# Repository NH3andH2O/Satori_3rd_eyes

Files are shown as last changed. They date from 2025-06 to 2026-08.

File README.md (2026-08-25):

English | [简体中文](README_zh-cn.md) | [繁體中文](README_zh-tw.md) | [日本語](README_ja.md)

# Mechanical Satori's Third Eye

A mechanical version of Satori Komeiji's third eye from Touhou Project. It currently supports gyroscope tracking and web-based control.

## Demo

https://www.bilibili.com/video/BV137yHB4ERo

## Authors and Licenses

- Code: 一水合氨基酸 (NH3andH2O), licensed under `Apache-2.0`
- 3D models
    - Third-eye assembly `3rd_eyes`: 牧鈴華SUZUKA. The original author granted permission to upload it to this GitHub repository. Contact the original author before using it for any other purpose ([project page](https://www.bilibili.com/video/BV1rN1gYJE3K)).
    - Heart-shaped accessory `heart_shaped`: 一水合氨基酸, licensed under `CC BY 4.0`
- PCD
    - `3rd_eyes`: Modified from a design by R饼锐度不够, licensed under `CC BY-NC-SA 3.0` ([project page](https://oshwhub.com/flanker-e/jue-zhi-tong-esp32))
    - `GC9A01`: 一水合氨基酸, licensed under `CC BY-NC-SA 3.0`

## Asset Credits

- Third-eye web interface icon: 幽蝶_Zomgel

## Project Structure

- `3d_model`: 3D models
- `pcd`: PCD design files
- `code`: Source code
- `tools`: Tools for debugging device sensors

## Getting Started

Download this repository and read the README in each directory.  
Recommended order: [pcd](pcd/README.md) → [3d_model](3d_model/README.md) → [code](code/README.md)

## Controls

- After uploading the firmware, the device enters gyroscope-tracking mode by default. Attach the heart-shaped accessory to your head and secure the third eye to your body to control it.
- To change the settings, connect to the `3rd-Eyes` Wi-Fi network (no password), then open `3rdeyes.local` to change the control mode and settings.

## Roadmap

- Add autonomous third-eye movements, such as blinking and head shaking
- Add controller support

## Contact

Join the project QQ group: `727559409`

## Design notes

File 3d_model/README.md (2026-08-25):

English | [简体中文](README_zh-cn.md) | [繁體中文](README_zh-tw.md) | [日本語](README_ja.md)

# Mechanical Satori's Third Eye Models

## Other Authors

- **3rd_eyes:** 牧鈴華SUZUKA ([project page](https://www.bilibili.com/video/BV1rN1gYJE3K))

## Usage

Print all `.stl` files with a 3D printer, then assemble them with reference to `STR-rc.prt`.

## Notes

- **Servos:** Use MG90S 180-degree servos. Center them at 90 degrees before installation.
  1. Use the program to move each servo to its center position.
     > [!TIP]
     > After flashing the main firmware, open the third-eye calibration page in the web interface and set all three servos to 90 degrees before installing the servo horns and gears.
  2. Install the servo horns and gears as shown below:  
     \
     Upper-eyelid servo horn position

     \
     Eyeball servo horn position. The servo horn should be perpendicular to the servo.

      \
     Lower-eyelid gear position. First adjust the gear shaft (yellow area) so that the rod notch faces directly outward, as indicated by the blue mark, and then mesh it with the gear on the servo.
- **About `pupil_GC9A01.prt`:** This is a slotted version of `pupil.prt`. A round transparent acrylic sheet with a thickness of `0.5 mm` and a diameter of `26.8 mm` can be fitted into the center.
- **About `heartShaped_dowm.prt`:** The bottom has mounting holes and can be secured to a headpiece with cable ties.

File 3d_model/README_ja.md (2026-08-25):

[English](README.md) | [简体中文](README_zh-cn.md) | [繁體中文](README_zh-tw.md) | 日本語

# 機械式サードアイのモデル

## その他の作者

- **3rd_eyes：** 牧鈴華SUZUKA（[プロジェクトページ](https://www.bilibili.com/video/BV1rN1gYJE3K)）

## 使用方法

すべての `.stl` ファイルを 3D プリンターで出力し、`STR-rc.prt` を参照して組み立ててください。

## 注意事項

- **サーボ：** MG90S 180 度サーボを使用します。取り付ける前に 90 度の中央位置に合わせてください。
  1. プログラムを使用してサーボを中央位置に移動します。
     > [!TIP]
     > メインファームウェアを書き込んだ後、Web インターフェースのサードアイ調整ページを開き、3 個のサーボを 90 度に設定してからサーボホーンとギアを取り付けることもできます。
  2. 次の図に従ってサーボホーンとギアを取り付けます。  
       \
     上まぶた用サーボホーンの取り付け位置

       \
     眼球用サーボホーンの取り付け位置。サーボホーンがサーボに対して垂直になるようにしてください。

       \
     下まぶた用ギアの取り付け位置。最初にギア軸（黄色の領域）の向きを調整し、ロッドの切り欠きが青い印のように真外側を向くようにしてから、サーボ側のギアとかみ合わせてください。
- **`pupil_GC9A01.prt` について：** `pupil.prt` の中央に溝を設けたバージョンです。厚さ `0.5 mm`、直径 `26.8 mm` の円形透明アクリル板を中央に取り付けられます。
- **`heartShaped_dowm.prt` について：** 底面に取り付け穴があり、結束バンドで髪飾りに固定できます。

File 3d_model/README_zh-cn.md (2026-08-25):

[English](README.md) | 简体中文 | [繁體中文](README_zh-tw.md) | [日本語](README_ja.md)

# 机械觉之瞳模型

## 其他作者

- **3rd_eyes：** 牧鈴華SUZUKA（[项目地址](https://www.bilibili.com/video/BV1rN1gYJE3K)）

## 如何使用

使用 3D 打印机打印所有 `.stl` 文件，然后参照 `STR-rc.prt` 进行安装。

## 注意事项

- **舵机：** 使用 MG90S 180 度舵机。安装前需要先将舵机居中至 90 度。
  1. 使用程序让舵机处于居中位置。
     > [!TIP]
     > 可以先烧录主程序，再通过网页进入觉之瞳校正页面，将 3 个舵机的角度设置为 90 度，然后安装舵臂和齿轮。
  2. 按照下图安装舵臂和齿轮：  
       \
     上眼皮舵臂安装位置

       \
     眼球舵臂安装位置。舵臂应与舵机保持垂直。

       \
     下眼皮齿轮安装位置。请先调整齿轮轴（黄色区域）的方向，使杆件缺口朝向正外侧（如蓝色标记所示），再与舵机上的齿轮啮合。
- **关于 `pupil_GC9A01.prt`：** 这是 `pupil.prt` 的中间开槽版本，可在中间放入厚度为 `0.5 mm`、直径为 `26.8 mm` 的圆形透明亚克力板（可在淘宝定制）。
- **关于 `heartShaped_dowm.prt`：** 底面设有开孔，可以使用扎带固定在头饰上。

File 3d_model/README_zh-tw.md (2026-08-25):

[English](README.md) | [简体中文](README_zh-cn.md) | 繁體中文 | [日本語](README_ja.md)

# 機械覺之瞳模型

## 其他作者

- **3rd_eyes：** 牧鈴華SUZUKA（[專案頁面](https://www.bilibili.com/video/BV1rN1gYJE3K)）

## 使用方法

使用 3D 印表機列印所有 `.stl` 檔案，然後參照 `STR-rc.prt` 進行組裝。

## 注意事項

- **伺服馬達：** 使用 MG90S 180 度伺服馬達。安裝前需先將伺服馬達置中至 90 度。
  1. 使用程式讓伺服馬達移動至置中位置。
     > [!TIP]
     > 可以先燒錄主程式，再透過網頁進入覺之瞳校正頁面，將 3 個伺服馬達的角度設為 90 度，然後安裝伺服擺臂及齒輪。
  2. 按照下圖安裝伺服擺臂及齒輪：  
       \
     上眼皮伺服擺臂安裝位置

       \
     眼球伺服擺臂安裝位置。伺服擺臂應與伺服馬達保持垂直。

       \
     下眼皮齒輪安裝位置。請先調整齒輪軸（黃色區域）的方向，使桿件缺口朝向正外側（如藍色標記所示），再與伺服馬達上的齒輪嚙合。
- **關於 `pupil_GC9A01.prt`：** 這是 `pupil.prt` 的中央開槽版本，可在中央放入厚度為 `0.5 mm`、直徑為 `26.8 mm` 的圓形透明壓克力板。
- **關於 `heartShaped_dowm.prt`：** 底面設有開孔，可以使用束帶固定在頭飾上。

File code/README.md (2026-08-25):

English | [简体中文](README_zh-cn.md) | [繁體中文](README_zh-tw.md) | [日本語](README_ja.md)

# Mechanical Satori's Third Eye Code

This directory contains the project's source code and development resources. It is divided into the following components:

- `3rd_eyes`: ESP32-S3 firmware for eye control, sensor processing, and communication
- `3rd_eyes_web`: Web control interface for configuration and interaction

## Directory Structure

- `3rd_eyes/`
  - Firmware source code, PlatformIO configuration, partition table, and tests
- `3rd_eyes_web/`
  - Vue/Vite web frontend

## Build Instructions

### 3rd_eyes_web

#### Build

1. Install [Node.js](https://nodejs.org/en/download).
   - After installation, open a terminal and verify it with:
     ```
     node -v
     npm -v
     ```
     If version numbers are displayed, the installation was successful.
2. Install dependencies.
   - Open a terminal in this directory and run `npm install`.
3. Build the project.
   - Run `npm run build`. After the build completes, a `data` directory will be generated under `code\3rd_eyes`, allowing the web interface to be uploaded to the development board.

#### Development

[VS Code](https://code.visualstudio.com) with [Dev Containers](https://marketplace.visualstudio.com/items?itemName=ms-vscode-remote.remote-containers) is recommended for development. You may also need to install and configure [Docker](https://www.docker.com).

### 3rd_eyes

#### Build

1. Install [VS Code](https://code.visualstudio.com).
2. Install the [PlatformIO IDE](https://marketplace.visualstudio.com/items?itemName=platformio.platformio-ide) extension and wait for the installation to finish.
3. Connect the development board to the computer. Click `Set upload/monitor/test port` at the bottom of the window (the plug-shaped icon), then select the serial port of the connected board.
4. Click the `PlatformIO` icon in the left sidebar, then select `esp32_s3_n16r8/General/Upload` under `PROJECT TASKS` to upload the firmware.
5. After building the web interface in `3rd_eyes_web` (a `data` directory should appear in this directory), select `esp32_s3_n16r8/Platform/Upload Filesystem Image` under `PROJECT TASKS` to upload it.

#### Serial Debugging Commands

The project provides serial debugging commands on UART0 at a default baud rate of `115200`. Send commands through the PlatformIO serial monitor or another serial terminal, followed by Enter.

Available commands:

- `help`: Display the supported serial commands.
- `reset`: Restart the device.
- `reservo`: Clear the saved servo configuration and switch to servo debugging mode.
- `mode [mode number]`: Change the operating mode:
  - `0`: Servo debugging mode.
  - `1`: Gyroscope-tracking mode.
  - `2`: Network control mode.
- `log [log level]`: Set and save the log level:
  - `1`: Error.
  - `2`: Warning.
  - `3`: Info.
  - `4`: Debug.
  - `5`: Verbose.

#### Notes

##### ESP32 Module Selection

This project uses the ESP32-S3-WROOM-1-N16R8 module with 16 MB QuadSPI Flash and 8 MB OctalSPI PSRAM.

- If your module does not have 16 MB of flash, update the partition table configuration in `partitions\n16r8.csv`.
- If your module does not have PSRAM, remove the following line from `platformio.ini`:
  ```
  -D BOARD_HAS_PSRAM
  ```

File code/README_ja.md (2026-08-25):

[English](README.md) | [简体中文](README_zh-cn.md) | [繁體中文](README_zh-tw.md) | 日本語

# 機械式サードアイのコード

このディレクトリには、プロジェクトのソースコードと開発用リソースが含まれています。主な構成は次のとおりです。

- `3rd_eyes`：目の制御、センサー処理、通信を担当する ESP32-S3 ファームウェア
- `3rd_eyes_web`：設定と操作に使用する Web コントロール画面

## ディレクトリ構成

- `3rd_eyes/`
  - ファームウェアのソースコード、PlatformIO 設定、パーティションテーブル、テストコード
- `3rd_eyes_web/`
  - Vue/Vite で構築された Web フロントエンド

## ビルド手順

### 3rd_eyes_web

#### ビルド

1. [Node.js](https://nodejs.org/ja/download) をインストールします。
   - インストール後、ターミナルを開いて次のコマンドで確認します。
     ```
     node -v
     npm -v
     ```
     バージョン番号が表示されれば、インストールは完了です。
2. 依存関係をインストールします。
   - ターミナルでこのディレクトリを開き、`npm install` を実行します。
3. プロジェクトをビルドします。
   - `npm run build` を実行します。ビルドが完了すると `code\3rd_eyes` フォルダー内に `data` フォルダーが生成され、Web インターフェースを開発ボードへアップロードできるようになります。

#### 開発

開発には [VS Code](https://code.visualstudio.com) と [Dev Containers](https://marketplace.visualstudio.com/items?itemName=ms-vscode-remote.remote-containers) の使用を推奨します。[Docker](https://www.docker.com) のインストールと設定も必要になる場合があります。

### 3rd_eyes

#### ビルド

1. [VS Code](https://code.visualstudio.com) をインストールします。
2. [PlatformIO IDE](https://marketplace.visualstudio.com/items?itemName=platformio.platformio-ide) 拡張機能をインストールし、完了するまで待ちます。
3. 開発ボードをコンピューターに接続します。ウィンドウ下部の `Set upload/monitor/test port`（プラグのようなアイコン）をクリックし、接続したボードのシリアルポートを選択します。
4. 左側の `PlatformIO` アイコンをクリックし、`PROJECT TASKS` から `esp32_s3_n16r8/General/Upload` を選択してファームウェアをアップロードします。
5. `3rd_eyes_web` フォルダーで Web インターフェースをビルドした後（このディレクトリに `data` フォルダーが表示されます）、`PROJECT TASKS` から `esp32_s3_n16r8/Platform/Upload Filesystem Image` を選択してアップロードします。

#### シリアルデバッグコマンド

このプロジェクトは UART0 でシリアルデバッグコマンドを提供し、デフォルトのボーレートは `115200` です。PlatformIO のシリアルモニターまたはその他のシリアルターミナルからコマンドを送信し、最後に Enter キーを押してください。

使用可能なコマンド：

- `help`：対応しているシリアルコマンドを表示します。
- `reset`：デバイスを再起動します。
- `reservo`：保存済みのサーボ設定を消去し、サーボデバッグモードに切り替えます。
- `mode [モード番号]`：動作モードを切り替えます。
  - `0`：サーボデバッグモード。
  - `1`：ジャイロ追従モード。
  - `2`：ネットワーク制御モード。
- `log [ログレベル]`：ログレベルを設定して保存します。
  - `1`：エラー（Error）。
  - `2`：警告（Warning）。
  - `3`：情報（Info）。
  - `4`：デバッグ（Debug）。
  - `5`：詳細（Verbose）。

#### 注意事項

##### ESP32 モジュールの選択

このプロジェクトでは、16 MB QuadSPI Flash と 8 MB OctalSPI PSRAM を搭載した ESP32-S3-WROOM-1-N16R8 モジュールを使用します。

- 購入したモジュールの Flash が 16 MB 版ではない場合、`partitions\n16r8.csv` のパーティションテーブル設定を変更してください。
- 購入したモジュールに PSRAM がない場合、`platformio.ini` から次の行を削除してください。
  ```
  -D BOARD_HAS_PSRAM
  ```

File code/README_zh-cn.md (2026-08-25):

[English](README.md) | 简体中文 | [繁體中文](README_zh-tw.md) | [日本語](README_ja.md)

# 机械觉之瞳代码说明

本目录包含该项目的代码及相关开发资源，主要分为以下部分：

- `3rd_eyes`：ESP32-S3 固件代码，负责眼睛控制、传感器处理及通信
- `3rd_eyes_web`：网页控制端代码，用于配置和交互

## 目录结构

- `3rd_eyes/`
  - 固件源代码、PlatformIO 配置、分区表及测试代码
- `3rd_eyes_web/`
  - 使用 Vue/Vite 构建的网页前端代码

## 构建说明

### 3rd_eyes_web

#### 构建

1. 安装 [Node.js](https://nodejs.org/zh-cn/download)。
   - 安装完成后，打开终端并输入以下命令进行确认：
     ```
     node -v
     npm -v
     ```
     如果能看到版本号，说明安装成功。
2. 安装依赖。
   - 使用终端进入本目录，执行 `npm install` 安装依赖。
3. 构建项目。
   - 执行 `npm run build` 构建项目。构建完成后，将在 `code\3rd_eyes` 文件夹下生成 `data` 文件夹，之后即可将网页代码上传到开发板。

#### 开发

建议使用 [VS Code](https://code.visualstudio.com) 和 [Dev Containers](https://marketplace.visualstudio.com/items?itemName=ms-vscode-remote.remote-containers) 进行开发。你可能还需要安装并配置 [Docker](https://www.docker.com)。

### 3rd_eyes

#### 构建

1. 安装 [VS Code](https://code.visualstudio.com)。
   - 可选：安装[简体中文](https://marketplace.visualstudio.com/items?itemName=MS-CEINTL.vscode-language-pack-zh-hans)语言包。
2. 安装 [PlatformIO IDE](https://marketplace.visualstudio.com/items?itemName=platformio.platformio-ide) 扩展，并等待安装完成。
3. 将开发板连接至电脑，点击窗口底部的 `Set upload/monitor/test port`（类似插头的图标），然后选择刚连接的开发板串口。
4. 点击左侧的 `PlatformIO` 图标，然后在 `PROJECT TASKS` 中选择 `esp32_s3_n16r8/General/Upload` 上传程序。
5. 在 `3rd_eyes_web` 文件夹中构建网页代码后（此目录下应出现 `data` 文件夹），在 `PROJECT TASKS` 中选择 `esp32_s3_n16r8/Platform/Upload Filesystem Image` 上传网页程序。

#### 串口调试命令

本项目在 UART0 上提供串口调试命令，默认波特率为 `115200`。可以通过 PlatformIO 串口监视器或其他串口工具发送命令，并在命令末尾按 Enter。

可用命令如下：

- `help`：显示当前支持的串口命令。
- `reset`：重启设备。
- `reservo`：清除已保存的舵机配置，并切换至舵机调试模式。
- `mode [模式编号]`：切换运行模式：
  - `0`：舵机调试模式。
  - `1`：陀螺仪跟踪模式。
  - `2`：网络控制模式。
- `log [日志等级]`：设置并保存日志等级：
  - `1`：错误（Error）。
  - `2`：警告（Warning）。
  - `3`：信息（Info）。
  - `4`：调试（Debug）。
  - `5`：详细（Verbose）。

#### 注意事项

##### ESP32 模组选择

本项目使用 ESP32-S3-WROOM-1-N16R8 模组，配备 16 MB QuadSPI Flash 和 8 MB OctalSPI PSRAM。

- 如果购买的模组 Flash 不是 16 MB 版本，需要修改 `partitions\n16r8.csv` 分区表配置。
- 如果购买的模组没有 PSRAM，需要在 `platformio.ini` 配置文件中删除以下语句：
  ```
  -D BOARD_HAS_PSRAM
  ```

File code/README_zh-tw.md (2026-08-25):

[English](README.md) | [简体中文](README_zh-cn.md) | 繁體中文 | [日本語](README_ja.md)

# 機械覺之瞳程式碼說明

本目錄包含此專案的程式碼及相關開發資源，主要分為以下部分：

- `3rd_eyes`：ESP32-S3 韌體程式碼，負責眼睛控制、感測器處理及通訊
- `3rd_eyes_web`：網頁控制端程式碼，用於設定及互動

## 目錄結構

- `3rd_eyes/`
  - 韌體原始碼、PlatformIO 設定、分割區表及測試程式碼
- `3rd_eyes_web/`
  - 使用 Vue/Vite 建置的網頁前端程式碼

## 建置說明

### 3rd_eyes_web

#### 建置

1. 安裝 [Node.js](https://nodejs.org/zh-tw/download)。
   - 安裝完成後，開啟終端機並輸入以下命令進行確認：
     ```
     node -v
     npm -v
     ```
     如果能看到版本號，表示安裝成功。
2. 安裝相依套件。
   - 使用終端機進入本目錄，執行 `npm install` 安裝相依套件。
3. 建置專案。
   - 執行 `npm run build` 建置專案。建置完成後，將在 `code\3rd_eyes` 資料夾下產生 `data` 資料夾，之後即可將網頁程式碼上傳至開發板。

#### 開發

建議使用 [VS Code](https://code.visualstudio.com) 及 [Dev Containers](https://marketplace.visualstudio.com/items?itemName=ms-vscode-remote.remote-containers) 進行開發。可能還需要安裝並設定 [Docker](https://www.docker.com)。

### 3rd_eyes

#### 建置

1. 安裝 [VS Code](https://code.visualstudio.com)。
2. 安裝 [PlatformIO IDE](https://marketplace.visualstudio.com/items?itemName=platformio.platformio-ide) 擴充套件，並等待安裝完成。
3. 將開發板連接至電腦，點選視窗底部的 `Set upload/monitor/test port`（類似插頭的圖示），然後選擇剛連接的開發板序列埠。
4. 點選左側的 `PlatformIO` 圖示，然後在 `PROJECT TASKS` 中選擇 `esp32_s3_n16r8/General/Upload` 上傳程式。
5. 在 `3rd_eyes_web` 資料夾中建置網頁程式碼後（本目錄下應出現 `data` 資料夾），在 `PROJECT TASKS` 中選擇 `esp32_s3_n16r8/Platform/Upload Filesystem Image` 上傳網頁程式。

#### 序列埠除錯命令

本專案在 UART0 上提供序列埠除錯命令，預設鮑率為 `115200`。可以透過 PlatformIO 序列埠監視器或其他序列埠工具傳送命令，並在命令末尾按下 Enter。

可用命令如下：

- `help`：顯示目前支援的序列埠命令。
- `reset`：重新啟動裝置。
- `reservo`：清除已儲存的伺服馬達設定，並切換至伺服馬達除錯模式。
- `mode [模式編號]`：切換執行模式：
  - `0`：伺服馬達除錯模式。
  - `1`：陀螺儀追蹤模式。
  - `2`：網路控制模式。
- `log [記錄層級]`：設定並儲存記錄層級：
  - `1`：錯誤（Error）。
  - `2`：警告（Warning）。
  - `3`：資訊（Info）。
  - `4`：除錯（Debug）。
  - `5`：詳細（Verbose）。

#### 注意事項

##### ESP32 模組選擇

本專案使用 ESP32-S3-WROOM-1-N16R8 模組，配備 16 MB QuadSPI Flash 及 8 MB OctalSPI PSRAM。

- 如果購買的模組 Flash 不是 16 MB 版本，需要修改 `partitions\n16r8.csv` 分割區表設定。
- 如果購買的模組沒有 PSRAM，需要在 `platformio.ini` 設定檔中刪除以下敘述：
  ```
  -D BOARD_HAS_PSRAM
  ```

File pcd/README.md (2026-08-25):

English | [简体中文](README_zh-cn.md) | [繁體中文](README_zh-tw.md) | [日本語](README_ja.md)

# Mechanical Satori's Third Eye PCD

## Other Authors

`3rd_eyes` is modified from a design by R饼锐度不够 ([project page](https://oshwhub.com/flanker-e/jue-zhi-tong-esp32)).

Main changes:

- Removed the camera module
- Added gyroscope modules
- Changed the servo I/O assignments
- Changed the GC9A01 ribbon-cable pin order
- Changed the 5 V-to-3.3 V converter inductor from _4.7 uH_ to _3.9 uH_

## Online Preview

https://oshwhub.com/nh3_h2o/satori_3rd_eyes

> [!WARNING]
> The online preview was converted from Altium Designer to EasyEDA for convenient viewing and has not been verified. Use the Gerber files when ordering boards.

## Usage

Send `3rd_eyes_GERBER.zip` and `GC9A01_GERBER.zip` directly to the PCB manufacturer.  
After the boards are manufactured, solder the components according to `3rd_eyes_BOM.csv` and `GC9A01_BOM.csv`.

## Notes

### ESP32-S3 Selection

`ESP32-S3-WROOM-1-N16R8` is recommended. Other module variants may require changes to the `platformIO` configuration.

### Gyroscope Selection and Setup

This project uses gyroscopes from WitMotion. The following models are recommended:

- **Eye gyroscope (mounted on the PCD):** A 6-axis gyroscope such as the [JY61P](https://www.wit-motion.cn/proztmz/37.html)
- **Head gyroscope (connected with Dupont wires):** A 9-axis gyroscope such as the [JY901S](https://www.wit-motion.cn/proztmz/22.html)

The main firmware configures some gyroscope settings automatically. The following setting must be configured with the [WitMotion PC software](https://wit-motion.yuque.com/wumwnr/aqvq6y/qngktvx5grz81zkq):

- Magnetic-field calibration (not required for 6-axis models; instructions should be available in the software)

Upload the main firmware first to apply the automatic gyroscope settings, then upload the `tools\witread` tool so the PC software can be used for configuration.

> [!NOTE]
> The gyroscopes do not need to be installed if the gyroscope features are not required.

### Head Gyroscope Connection

Solder the angled pin header supplied by the manufacturer to the UART side of the head gyroscope. Do not solder the I2C side.  
Use female-to-female Dupont wires connected to `H4`; a length of 60–80 cm is recommended.



### Power Switch Recommendation

Use a switch designed for a 7 mm keycap.

### Servo Connections

Use MG90S 180-degree servos and connect them to `H1`–`H3`.

> [!WARNING]
> The brand must be TIANKONGRC. Make sure the supplied servo horn is the version without reinforcing ribs.

### Display Connection

Use a bare GC9A01 display and solder it to `U1` on the `GC9A01` PCD.

> [!WARNING]
> Check the front and back orientation of the display pins before soldering. After soldering, the PCD should flip naturally so its back can be attached to the back of the display with double-sided tape.

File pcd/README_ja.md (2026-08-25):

[English](README.md) | [简体中文](README_zh-cn.md) | [繁體中文](README_zh-tw.md) | 日本語

# 機械式サードアイ PCD

## その他の作者

`3rd_eyes` は R饼锐度不够による設計を改変したものです（[プロジェクトページ](https://oshwhub.com/flanker-e/jue-zhi-tong-esp32)）。

主な変更点：

- カメラモジュールを削除
- ジャイロセンサーモジュールを追加
- サーボの I/O 割り当てを変更
- GC9A01 フラットケーブルのピン順を変更
- 5 V から 3.3 V への変換回路のインダクターを _4.7 uH_ から _3.9 uH_ に変更

## オンラインプレビュー

https://oshwhub.com/nh3_h2o/satori_3rd_eyes

> [!WARNING]
> オンラインプレビューは、閲覧しやすいように Altium Designer から EasyEDA に変換したもので、検証されていません。基板を発注する際は Gerber ファイルを使用してください。

## 使用方法

`3rd_eyes_GERBER.zip` と `GC9A01_GERBER.zip` を基板メーカーへ直接送付してください。  
基板の製造後、`3rd_eyes_BOM.csv` と `GC9A01_BOM.csv` に従って部品をはんだ付けします。

## 注意事項

### ESP32-S3 の選択

`ESP32-S3-WROOM-1-N16R8` を推奨します。その他のモジュールでは `platformIO` の設定変更が必要になる場合があります。

### ジャイロセンサーの選択と設定

このプロジェクトでは WitMotion 製ジャイロセンサーを使用します。次のモデルを推奨します。

- **目側（PCD 上のジャイロセンサー）：**[JY61P](https://www.wit-motion.cn/proztmz/37.html) などの 6 軸ジャイロセンサー
- **頭部側（ジャンパーワイヤーで接続するジャイロセンサー）：**[JY901S](https://www.wit-motion.cn/proztmz/22.html) などの 9 軸ジャイロセンサー

メインファームウェアは一部の設定を自動的に行いますが、次の項目は [WitMotion PC ソフトウェア](https://wit-motion.yuque.com/wumwnr/aqvq6y/qngktvx5grz81zkq)で設定する必要があります。

- 磁場キャリブレーション（6 軸モデルでは不要です。手順は PC ソフトウェア内の説明を参照してください）

最初にメインファームウェアをアップロードして自動設定を行い、その後 `tools\witread` ツールをアップロードして PC ソフトウェアから設定してください。

> [!NOTE]
> ジャイロ機能を使用しない場合、ジャイロセンサーを実装する必要はありません。

### 頭部ジャイロセンサーの接続

メーカー付属の曲がりピンヘッダーを、頭部ジャイロセンサーの UART 側にはんだ付けしてください。I2C 側にははんだ付けしないでください。  
メス－メスのジャンパーワイヤーで `H4` に接続します。長さは 60～80 cm を推奨します。



### 電源スイッチの推奨

7 mm キーキャップ対応のスイッチを推奨します。

### サーボの接続

MG90S 180 度サーボを使用し、`H1`～`H3` に接続します。

> [!WARNING]
> ブランドは TIANKONGRC を使用してください。付属のサーボホーンが補強リブなしのタイプであることも確認してください。

### ディスプレイの接続

ベアタイプの GC9A01 ディスプレイを使用し、`GC9A01` PCD の `U1` にはんだ付けします。

> [!WARNING]
> はんだ付け前にディスプレイ端子の表裏を確認してください。はんだ付け後、PCD を自然に折り返し、両面テープで PCD の裏面をディスプレイ基板の裏面に貼り付けられる向きにします。

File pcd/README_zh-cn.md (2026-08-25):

[English](README.md) | 简体中文 | [繁體中文](README_zh-tw.md) | [日本語](README_ja.md)

# 机械觉之瞳 PCD

## 其他作者

`3rd_eyes` 修改自 R饼锐度不够（[项目地址](https://oshwhub.com/flanker-e/jue-zhi-tong-esp32)）。

主要修改内容：

- 去除摄像头模组
- 添加陀螺仪模组
- 修改舵机 I/O
- 修改 GC9A01 排线顺序
- 将 5 V 转 3.3 V 电路的电感从 _4.7 uH_ 改为 _3.9 uH_

## 在线查看

https://oshwhub.com/nh3_h2o/satori_3rd_eyes

> [!WARNING]
> 在线版本由 Altium Designer 转换为嘉立创 EDA，仅供方便查看，且未经检查。如需制作电路板，请使用 Gerber 文件。

## 使用方法

将 `3rd_eyes_GERBER.zip` 和 `GC9A01_GERBER.zip` 直接发送给板厂。  
电路板制作完成后，根据 `3rd_eyes_BOM.csv` 和 `GC9A01_BOM.csv` 将零件焊接到板上。

## 注意事项

### ESP32-S3 选择

建议选择 `ESP32-S3-WROOM-1-N16R8`。其他版本的模组可能需要修改 `platformIO` 配置。

### 陀螺仪选择和使用

本项目使用“维特智能”系列陀螺仪，建议选择以下型号：

- **眼睛（PCD 上的陀螺仪）：**建议使用 6 轴陀螺仪，如 [JY61P](https://www.wit-motion.cn/proztmz/37.html)
- **头部（通过杜邦线连接的陀螺仪）：**建议使用 9 轴陀螺仪，如 [JY901S](https://www.wit-motion.cn/proztmz/22.html)

主程序会自动设置部分陀螺仪配置，但以下项目无法自动设置，需要使用[上位机软件](https://wit-motion.yuque.com/wumwnr/aqvq6y/qngktvx5grz81zkq)进行配置：

- 校正磁场（6 轴型号无需校正；上位机软件中应有校正教程）

先上传主程序以自动设置陀螺仪，再上传 `tools\witread` 工具，以便使用上位机软件进行配置。

> [!NOTE]
> 如果不需要使用陀螺仪功能，可以不焊接陀螺仪。

### 头部陀螺仪连接

将厂商附带的弯排针焊接在头部陀螺仪的 UART 一侧，请勿焊接 I2C 一侧。  
使用母对母杜邦线连接至 `H4`，建议长度为 60–80 cm。



### 电源开关选择建议

建议使用适配 7 mm 键帽的开关。

### 舵机连接

使用 MG90S 180 度舵机，分别连接至 `H1`–`H3`。

> [!WARNING]
> 品牌必须为 TIANKONGRC，并请确认所配舵臂是不带加强筋的型号。

### 屏幕连接

选择 GC9A01 裸屏，并将其焊接至 `GC9A01` PCD 上的 `U1`。

> [!WARNING]
> 焊接时请确认屏幕引脚的正反方向。焊接完成后，PCD 应能自然翻转，以便使用双面胶将 PCD 背面粘贴至显示屏背面。

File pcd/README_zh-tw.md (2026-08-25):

[English](README.md) | [简体中文](README_zh-cn.md) | 繁體中文 | [日本語](README_ja.md)

# 機械覺之瞳 PCD

## 其他作者

`3rd_eyes` 修改自 R饼锐度不够（[專案頁面](https://oshwhub.com/flanker-e/jue-zhi-tong-esp32)）。

主要修改內容：

- 移除相機模組
- 加入陀螺儀模組
- 修改伺服馬達 I/O
- 修改 GC9A01 排線順序
- 將 5 V 轉 3.3 V 電路的電感從 _4.7 uH_ 改為 _3.9 uH_

## 線上檢視

https://oshwhub.com/nh3_h2o/satori_3rd_eyes

> [!WARNING]
> 線上版本由 Altium Designer 轉換為嘉立創 EDA，僅供方便檢視，且未經檢查。如需製作電路板，請使用 Gerber 檔案。

## 使用方法

將 `3rd_eyes_GERBER.zip` 及 `GC9A01_GERBER.zip` 直接傳送給板廠。  
電路板製作完成後，依照 `3rd_eyes_BOM.csv` 及 `GC9A01_BOM.csv` 將零件焊接至板上。

## 注意事項

### ESP32-S3 選擇

建議選擇 `ESP32-S3-WROOM-1-N16R8`。其他版本的模組可能需要修改 `platformIO` 設定。

### 陀螺儀選擇及使用

本專案使用「維特智能」系列陀螺儀，建議選擇以下型號：

- **眼睛（PCD 上的陀螺儀）：**建議使用 6 軸陀螺儀，例如 [JY61P](https://www.wit-motion.cn/proztmz/37.html)
- **頭部（透過杜邦線連接的陀螺儀）：**建議使用 9 軸陀螺儀，例如 [JY901S](https://www.wit-motion.cn/proztmz/22.html)

主程式會自動設定部分陀螺儀參數，但以下項目無法自動設定，需要使用[上位機軟體](https://wit-motion.yuque.com/wumwnr/aqvq6y/qngktvx5grz81zkq)進行設定：

- 校正磁場（6 軸型號不需校正；上位機軟體中應有校正教學）

先上傳主程式以自動設定陀螺儀，再上傳 `tools\witread` 工具，以便使用上位機軟體進行設定。

> [!NOTE]
> 如果不需要使用陀螺儀功能，可以不焊接陀螺儀。

### 頭部陀螺儀連接

將廠商附帶的彎排針焊接在頭部陀螺儀的 UART 一側，請勿焊接 I2C 一側。  
使用母對母杜邦線連接至 `H4`，建議長度為 60–80 cm。



### 電源開關選擇建議

建議使用適用於 7 mm 鍵帽的開關。

### 伺服馬達連接

使用 MG90S 180 度伺服馬達，分別連接至 `H1`–`H3`。

> [!WARNING]
> 品牌必須為 TIANKONGRC，並請確認所附伺服擺臂是不含加強肋的型號。

### 螢幕連接

選擇 GC9A01 裸螢幕，並將其焊接至 `GC9A01` PCD 上的 `U1`。

> [!WARNING]
> 焊接時請確認螢幕接腳的正反方向。焊接完成後，PCD 應能自然翻轉，以便使用雙面膠將 PCD 背面黏貼至顯示器背面。

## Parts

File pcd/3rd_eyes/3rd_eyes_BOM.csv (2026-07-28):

Comment | Designator | Footprint | LibRef | Quantity
100nF | C1, C10, C11, C14 | C0603 | CL10B104KB8NNNC | 4
1uF | C2 | C0603 | CL10A105KB8NNNC | 1
22uF | C3, C4, C5, C6, C7, C8, C15, C16 | C0805 | CL21A226MAQNNNE | 8
10uF | C9, C12, C18 | C0603 | CL10A106MA8NRNC | 3
4.7uF | C13 | C0603 | CL10A475KO8NNNC | 1
2.2uF | C17 | C0603 | CL10A225KB8NNNC | 1
220uF | C19, C20, C21 | CAP-SMD_BD6.3-L6.6-W6.6-FD-A | OVZ221M0JTR-0606 | 3
SS14L | D1, D2 | SOD-123F_L2.8-W1.8-LS3.7-RD | SS14L | 2
12H1300C | F1 | F1206 | 12H1300C | 1
AFC01-S08FCA-00 | FPC1 | FPC-SMD_P0.50-8P_FGS-XJ-H2.0 | AFC01-S08FCA-00 | 1
PZ254V-11-03P | H1, H2, H3 | HDR-TH_3P-P2.54-V-M | PZ254V-11-03P | 3
PZ254V-11-04P | H4 | HDR-TH_4P-P2.54-V-M | PZ254V-11-04P_C492403 | 1
1uH | L1 | IND-SMD_L7.0-W6.6 | FXL0630-1R0-M | 1
3.9uH | L2 | IND-SMD_L4.0-W4.0_FNR40XXS | FNR4030S3R9MT | 1
NCD0603Y1 | LED1, LED2, LED3, LED4 | LED0603-RD | NCD0603Y1 | 4
SS8050 | Q1, Q2 | SOT-23-3_L2.9-W1.3-P1.90-LS2.4-BR | SS8050_C541705 | 2
10kΩ | R1, R2, R3, R4 | R0603 | 0603WAF1002T5E | 4
5.1kΩ | R5, R7 | R0603 | 0603WAF5101T5E | 2
500mΩ | R6 | R0805 | FRL0805JR500TS | 1
2Ω | R8 | R0603 | 0603WAF200KT5E | 1
100Ω | R9 | R0603 | 0603WAF1000T5E | 1
ESP32-S3-WROOM-1U-N16R8 | U1 | WIRELM-SMD_ESP32-S3-WROOM-1U | ESP32-S3-WROOM-1U-N16R8 | 1
IP5306 | U2 | ESOP-8_L4.9-W3.9-P1.27-LS6.0-BL-EP | IP5306 | 1
CH340C | U3 | SOP-16_L10.0-W3.9-P1.27-LS6.0-BL | CH340C | 1
KH-SS12F23-G6 | U4 | SW-TH_KH-SS12F23-G6 | KH-SS12F23-G6 | 1
IP3005A | U5 | ESOP-8_L4.9-W3.9-P1.27-LS6.0-BL-EP | IP3005A | 1
AP63203WU-7 | U7 | TSOT-26_L2.9-W1.6-P0.95-LS2.8-BL | AP63203WU-7 | 1
JY61P | U8 | JY61P | JY61P | 1
KH-TYPE-C-16P | USB1 | USB-C-SMD_KH-TYPE-C-16P | KH-TYPE-C-16P | 1

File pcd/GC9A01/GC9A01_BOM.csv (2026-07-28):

Comment | Designator | Footprint | LibRef | Quantity
100nF | C1 | C0603 | CL10B104KB8NNNC | 1
AFC01-S08FCA-00 | FPC1 | FPC-SMD_P0.50-8P_FGS-XJ-H2.0 | AFC01-S08FCA-00 | 1
SS8050 | Q1 | SOT-23-3_L2.9-W1.3-P1.90-LS2.4-BR | SS8050_C541705 | 1
10Ω | R1 | R0603 | 0603WAF100JT5E | 1
1kΩ | R2 | R0603 | 0603WAF1001T5E | 1
10kΩ | R3 | R0603 | 0603WAF1002T5E | 1
IPS130-12 | U1 | FPC_0.7-12P_SMT | IPS130-12 | 1

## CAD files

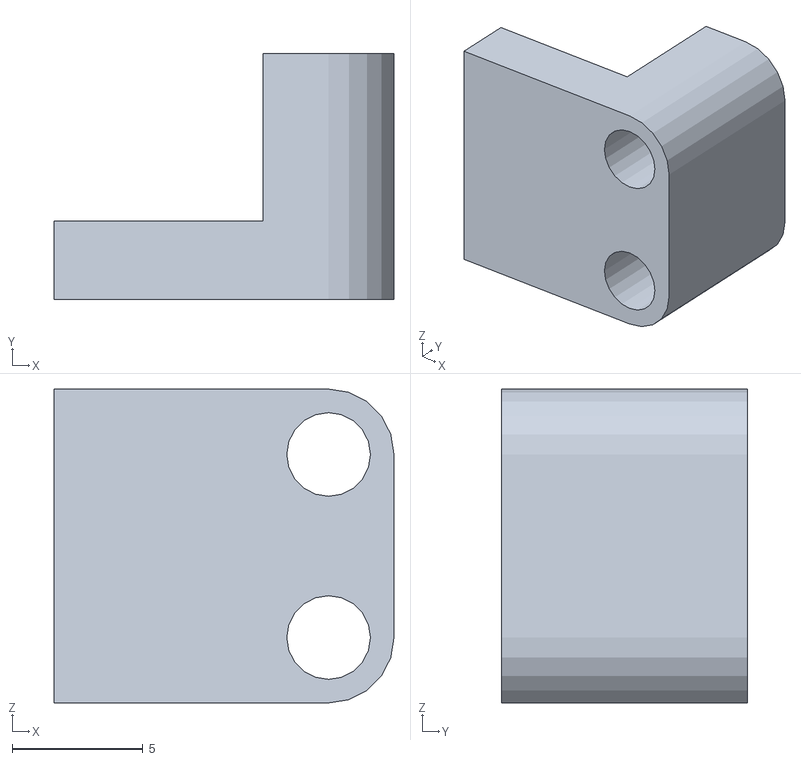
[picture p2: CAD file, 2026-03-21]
3d_model/3rd_eyes/stl/servo pin.stl
13.0 x 9.40 x 12.0

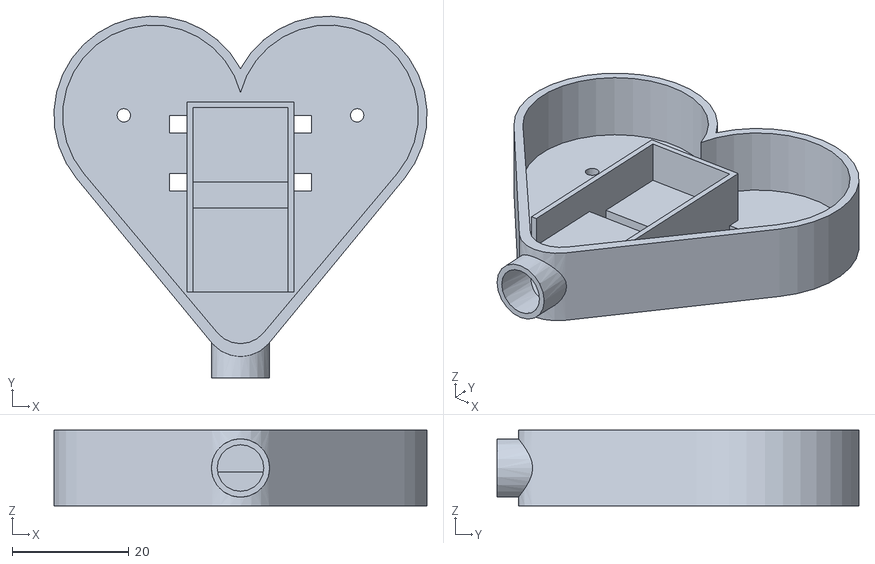
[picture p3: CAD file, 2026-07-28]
3d_model/heart_shaped/stl/heartShaped_dowm.stl
64.0 x 62.0 x 13.0

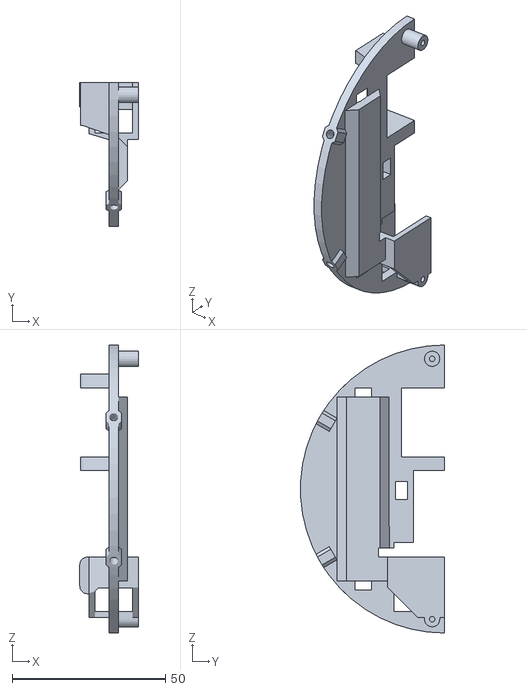
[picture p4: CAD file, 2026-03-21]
3d_model/3rd_eyes/stl/03-1.stl
19.1 x 46.9 x 94.0

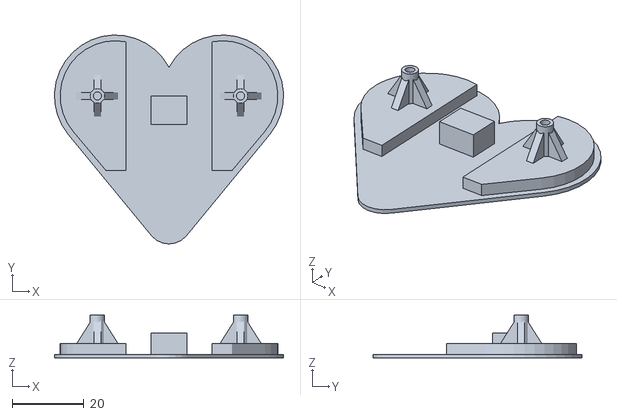
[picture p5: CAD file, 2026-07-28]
3d_model/heart_shaped/stl/heartShaped_up.stl
64.0 x 58.3 x 12.0

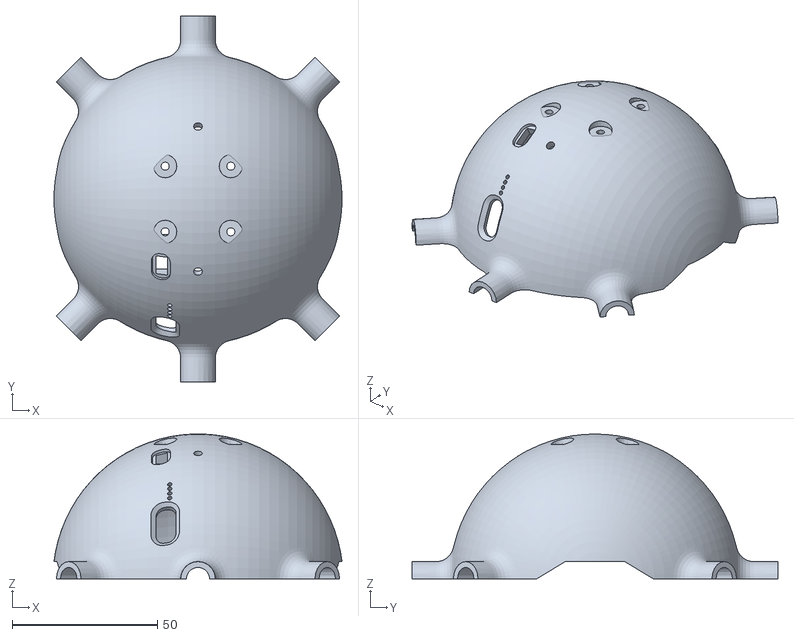
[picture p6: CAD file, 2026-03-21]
3d_model/3rd_eyes/stl/02.stl
99.3 x 126.0 x 50.0

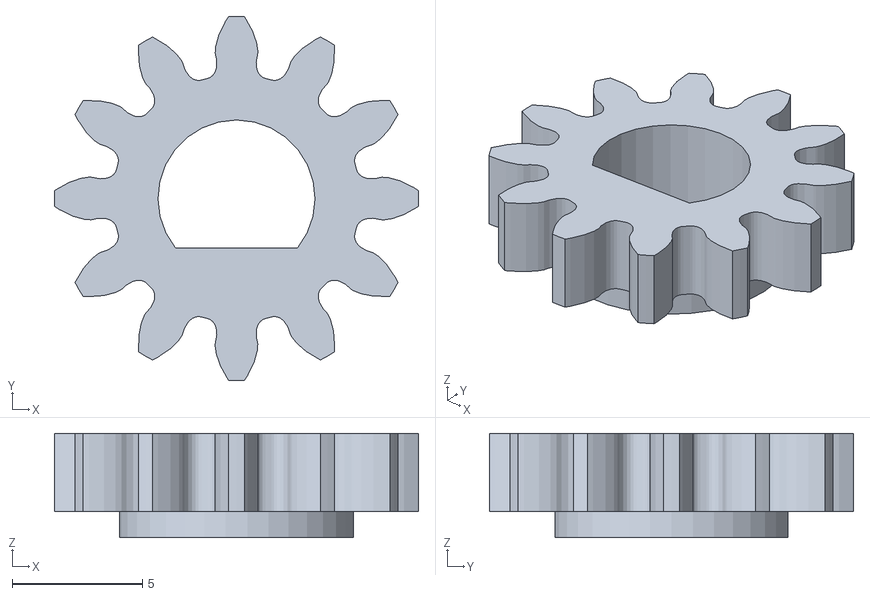
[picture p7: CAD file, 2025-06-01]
3d_model/3rd_eyes/stl/gear2.stl
14.0 x 14.0 x 4.00

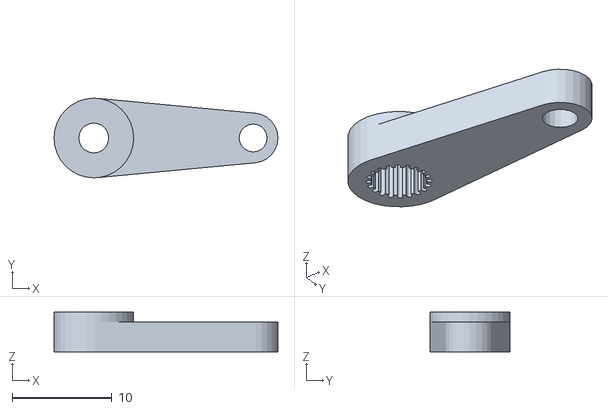
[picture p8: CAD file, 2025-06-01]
3d_model/3rd_eyes/stl/rocker.stl
22.5 x 8.00 x 4.00

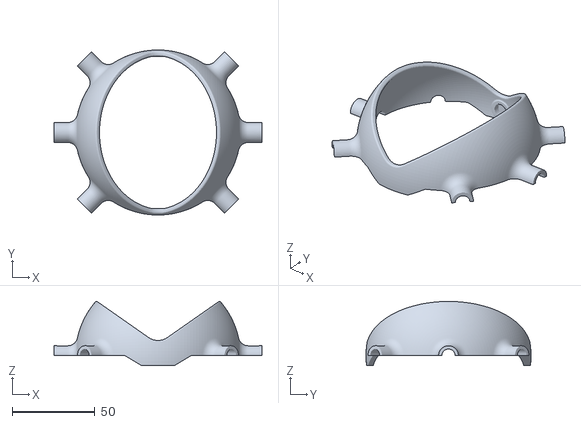
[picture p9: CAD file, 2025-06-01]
3d_model/3rd_eyes/stl/01.stl
126.0 x 100.0 x 38.8

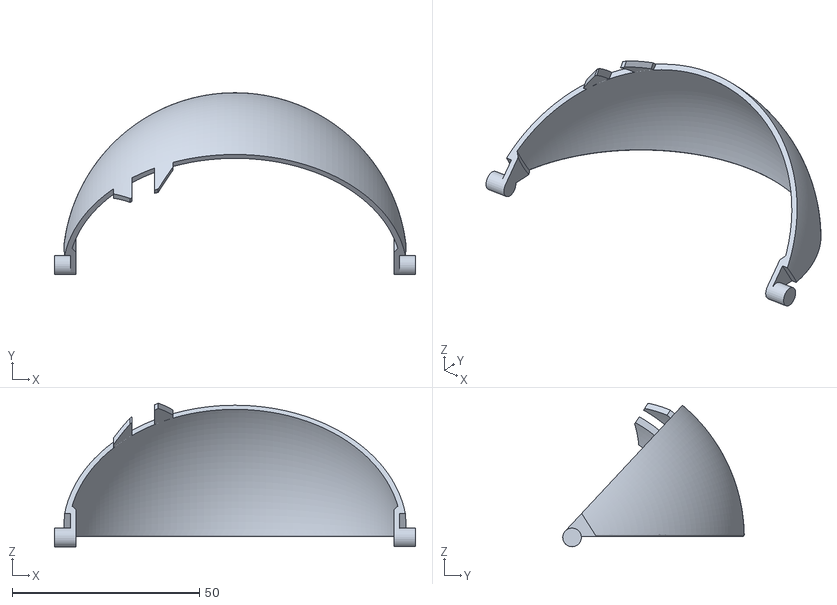
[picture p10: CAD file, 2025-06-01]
3d_model/3rd_eyes/stl/05.stl
96.4 x 48.5 x 38.3

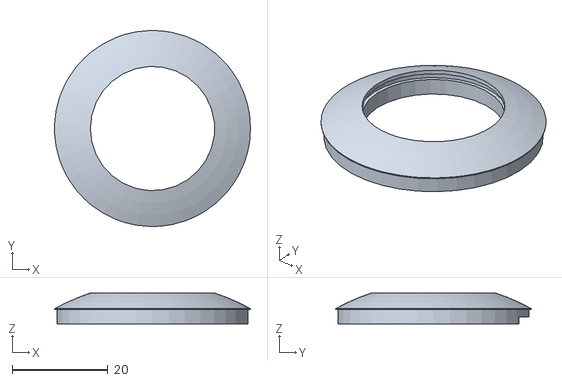
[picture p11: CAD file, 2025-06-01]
3d_model/3rd_eyes/stl/pupil_GC9A01.stl
41.0 x 41.0 x 6.48

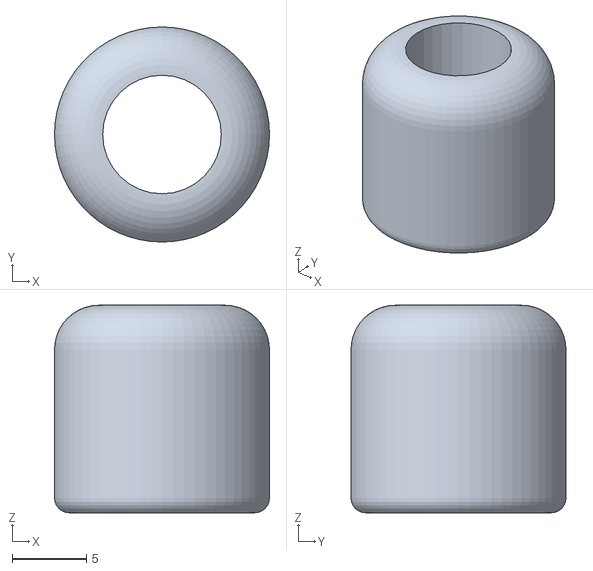
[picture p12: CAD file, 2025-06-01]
3d_model/3rd_eyes/stl/09(3).stl
14.5 x 14.5 x 14.0

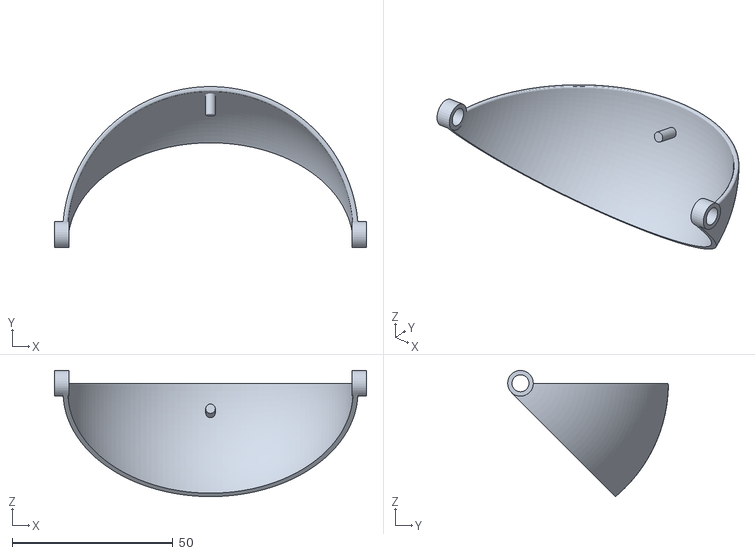
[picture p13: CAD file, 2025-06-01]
3d_model/3rd_eyes/stl/06.stl
97.0 x 50.0 x 39.2

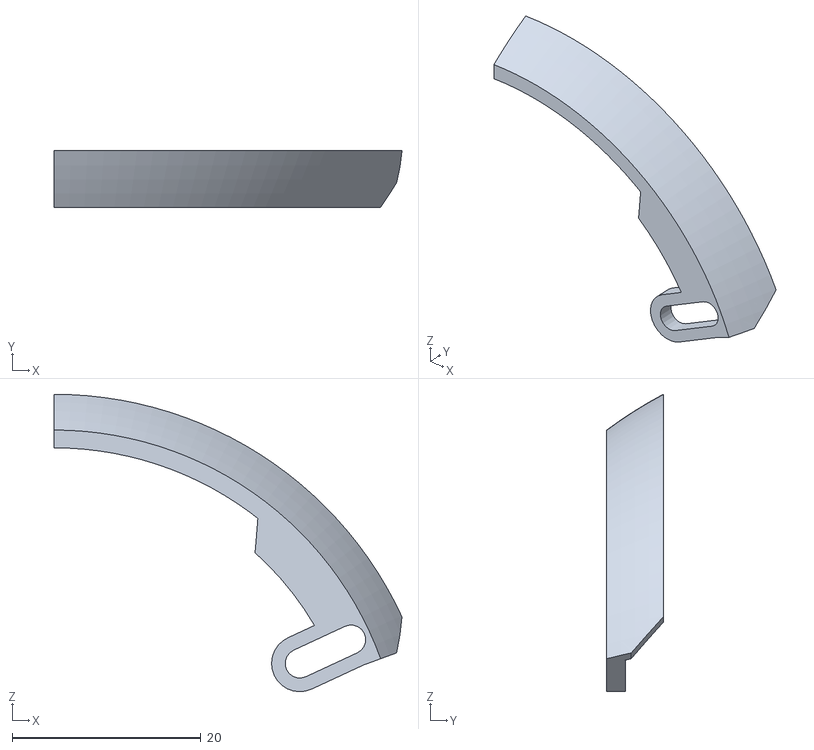
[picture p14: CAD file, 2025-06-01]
3d_model/3rd_eyes/stl/rack-rc.stl
36.9 x 6.00 x 31.6

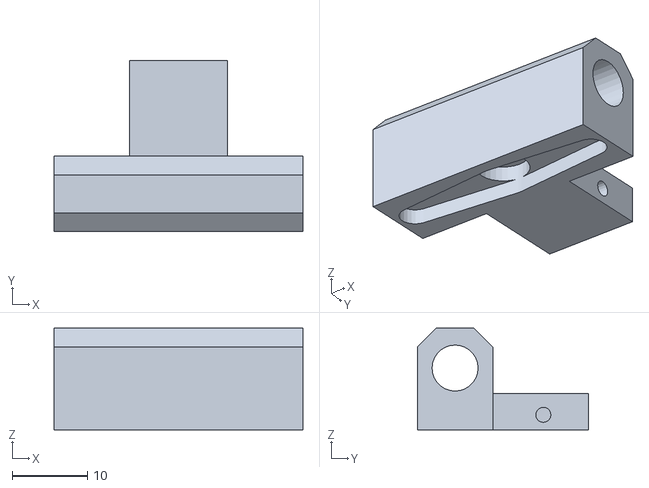
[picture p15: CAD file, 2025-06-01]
3d_model/3rd_eyes/stl/07.stl
33.0 x 22.7 x 13.5

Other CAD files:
3d_model/3rd_eyes/stl/08.stl
3d_model/3rd_eyes/stl/gear1.stl
3d_model/3rd_eyes/prt/01.prt
3d_model/3rd_eyes/prt/02.prt
3d_model/3rd_eyes/prt/03-1.prt
3d_model/3rd_eyes/prt/04.prt
3d_model/3rd_eyes/prt/05.prt
3d_model/3rd_eyes/prt/06.prt
3d_model/3rd_eyes/prt/07.prt
3d_model/3rd_eyes/prt/08.prt
3d_model/3rd_eyes/prt/09.prt
3d_model/3rd_eyes/prt/DCDC.prt
3d_model/3rd_eyes/prt/MG90S.prt
3d_model/3rd_eyes/prt/SS12F15VG6.prt
3d_model/3rd_eyes/prt/STR-rc.prt
3d_model/3rd_eyes/prt/YAOBI.prt
3d_model/3rd_eyes/prt/gear1.prt
3d_model/3rd_eyes/prt/gear2.prt
3d_model/3rd_eyes/prt/pad.prt
3d_model/3rd_eyes/prt/pupil.prt
3d_model/3rd_eyes/prt/pupil_GC9A01.prt
3d_model/3rd_eyes/prt/rack-rc.prt
3d_model/3rd_eyes/prt/rocker.prt
3d_model/3rd_eyes/prt/servo pin.prt
3d_model/3rd_eyes/prt/support-1.prt
3d_model/3rd_eyes/stl/04.stl
3d_model/3rd_eyes/stl/pupil.stl
3d_model/3rd_eyes/stl/support-1.stl
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

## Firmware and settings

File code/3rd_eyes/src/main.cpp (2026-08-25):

// Copyright 2025 NH3andH2O
//
// Licensed under the Apache License, Version 2.0 (the "License");
// you may not use this file except in compliance with the License.
// You may obtain a copy of the License at
//
//     http://www.apache.org/licenses/LICENSE-2.0
//
// Unless required by applicable law or agreed to in writing, software
// distributed under the License is distributed on an "AS IS" BASIS,
// WITHOUT WARRANTIES OR CONDITIONS OF ANY KIND, either express or implied.
// See the License for the specific language governing permissions and
// limitations under the License.
/* 第三方程式庫 */
#include <Arduino.h>
#include <ESP32Servo.h>
#include <LovyanGFX.hpp>
#include <Config.h>
#include <WiFi.h>
#include <ESPAsyncWebServer.h>
#include <FS.h>
#include <LittleFS.h>
#include <ESPmDNS.h>
#include <ArduinoJson.h>
#include <driver/uart.h>
#include <esp_log.h>
#include <esp_system.h>
#include <esp_wifi.h>
#include <freertos/event_groups.h>
#include <atomic>
/* 自定義程式庫 */
#include <gc9a01.h>
#include <eyesMove.h>
#include <wit.h>
#include <IMUAngle.h>
#include <serverResponse.h>
#include "types.h"

#define UPPER_EYELID_PIN 13 // 上眼皮伺服馬達引脚
#define LOWER_EYELID_PIN 14 // 下眼皮伺服馬達引脚
#define EYEBALL_PIN 21		// 眼球伺服馬達引脚

#define witEyes_RX_PIN 18 // wit眼睛模組RX引脚
#define witEyes_TX_PIN 8  // wit眼睛模組TX引脚
#define witHead_RX_PIN 39 // wit頭部模組RX引脚
#define witHead_TX_PIN 38 // wit頭部模組TX引脚

#define GC9A01_BLK_PIN 5  // GC9A01背光引脚
#define GC9A01_RST_PIN 15 // GC9A01重置引脚
#define GC9A01_CS_PIN 6	  // GC9A01片選引脚
#define GC9A01_DC_PIN 7	  // GC9A01數據/命令引脚
#define GC9A01_SCL_PIN 17 // GC9A01時鐘引脚
#define GC9A01_SDA_PIN 16 // GC9A01數據引脚

#define SERVO_SET_MODE 0		// 伺服馬達調試模式
#define GYROSCOPE_TRACKS_MODE 1 // 陀螺儀跟蹤模式
#define NETWORK_CONTROL_MODE 2	// 網絡控制模式

// 位元遮罩用於保留不同模式共用的任務
static constexpr uint8_t TASK_MASK_WIT = 0x01;
static constexpr uint8_t TASK_MASK_GYROSCOPE = 0x02;
static constexpr uint8_t TASK_MASK_NETWORK = 0x04;
static constexpr uint8_t TASK_MASK_SERVO_SET = 0x08;
static constexpr uint8_t TASK_MASK_EYES_MOVE = 0x10;
// WIT 任務僅在關閉 UART 後回報停止
static constexpr EventBits_t WIT_EYES_STOPPED_BIT = BIT0;
static constexpr EventBits_t WIT_HEAD_STOPPED_BIT = BIT1;
static constexpr uint32_t WIT_STOP_TIMEOUT_MS = 1500;

/** 函數宣告 **/
/* 事件函數宣告 */
void WiFiEvent(WiFiEvent_t event, WiFiEventInfo_t info); // WiFi事件處理函數

/* 回調函數宣告 */
void TimerReconnectWiFi(TimerHandle_t xTimer); // WiFi重連定時器回調函數

/* 任務函數宣告 */
void taskNetwork(void *pvParameters);		 // 網絡任務
void taskWebServer(void *pvParameters);		 // Web服務器任務
void taskModeManagement(void *pvParameters); // 模式管理任務
void taskWitGetData(void *arg);				 // 獲取wit數據任務
void taskWitPProcessingData(void *arg);		 // 處理wit數據任務
void taskGyroscopeTracking(void *arg);		 // 陀螺儀跟蹤任務
void taskNetworkControl(void *arg);			 // 網絡控制任務
void taskNetworkControlGC9A01(void *arg);	 // 網絡控制屏幕任務
void taskGC9A01(void *arg);					 // GC9A01任務
void taskEyesMove(void *arg);				 // 眼睛任務
void taskUART0Read(void *arg);				 // UART0讀取任務
void taskServoSet(void *arg);				 // 伺服馬達調試任務

/* 其他函數宣告 */
void queueCreate(QueueHandle_t *quene, uint8_t queneSize, uint8_t queneType); // 佇列創建
void TaskDeleteSafe(TaskHandle_t *pHandle, uint32_t yieldMs = 0);
bool TaskCreateSafe(TaskFunction_t task, const char *name, uint32_t stackSize, void *parameter, UBaseType_t priority, TaskHandle_t *handle,
					BaseType_t core);
bool GetModeTaskMask(int8_t mode, uint8_t *taskMask);
bool StopWitTasks();
void ResetModeQueues();
void StopAllModeTasks();
bool ConnectMeshWiFi(const AppConfig::WiFiConfig &wifiConfig);
bool StartSoftAP(const AppConfig::SoftAPConfig &softAPConfig);
void ScheduleWiFiReconnect(uint8_t reason);
String macToString(const uint8_t mac[6]); // MAC地址轉字符串

/* 結構體宣告 */
eyesMove eyesmove(UPPER_EYELID_PIN, LOWER_EYELID_PIN, EYEBALL_PIN);

wit witEyes(SERIAL1, witEyes_RX_PIN, witEyes_TX_PIN, 115200, 6, 1); // wit眼睛模組
wit witHead(SERIAL2, witHead_RX_PIN, witHead_TX_PIN, 115200, 9, 0); // wit頭部模組

GC9A01 gc9a01(GC9A01_SDA_PIN, GC9A01_SCL_PIN, GC9A01_CS_PIN, GC9A01_DC_PIN, GC9A01_RST_PIN, GC9A01_BLK_PIN); // GC9A01實例

AppConfig::Config config; // 配置實例

AsyncWebServer server(80); // Web服務器
AsyncWebSocket ws("/ws");  // WebSocket服務器

witData witEyes_data; // wit眼睛數據結構體
witData witHead_data; // wit頭部數據結構體

/* 佇列宣告 */
QueueHandle_t wit_data_quene;					// 宣告wit原始佇列
QueueHandle_t wit_data_relative_angle_quene;	// 宣告wit差值佇列
QueueHandle_t eyesmove_data_quene;				// 宣告眼睛數據佇列
QueueHandle_t gc9a01_data_quene;				// 宣告GC9A01佇列
QueueHandle_t wifiUpdate_data_quene;			// 宣告WiFi更新佇列
QueueHandle_t wit_advanced_config_update_quene; // 每個consumer必須使用獨立佇列
QueueHandle_t gyroscope_advanced_config_update_quene;
QueueHandle_t mode_data_quene;					// 宣告模式數據佇列
QueueHandle_t uart0_queue;						// UART0事件佇列
QueueHandle_t network_control_data_quene;		// 網絡數據佇列
QueueHandle_t network_control_speed_data_quene; // 網絡控制速度數據佇列
QueueHandle_t servoSet_data_quene;				// 伺服馬達調試數據佇列
EventGroupHandle_t witStopEventGroup = nullptr; // WIT 安全停止回報

/* 任務參照 */
TaskHandle_t taskWitEyesGetData_handle = nullptr;		// 獲取wit眼睛數據任務
TaskHandle_t taskWitHeadGetData_handle = nullptr;		// 獲取wit頭部數據任務
TaskHandle_t taskWitPProcessingData_handle = nullptr;	// 處理wit數據任務
TaskHandle_t taskGyroscopeTracking_handle = nullptr;	// 陀螺儀跟蹤任務
TaskHandle_t taskNetworkControl_handle = nullptr;		// 網絡控制任務
TaskHandle_t taskNetworkControlGC9A01_handle = nullptr; // 網絡控制屏幕任務
TaskHandle_t taskGC9A01_handle = nullptr;				// GC9A01任務
TaskHandle_t taskEyesMove_handle = nullptr;				// 眼睛任務
TaskHandle_t taskWebServer_handle = nullptr;			// Web服務器任務
TaskHandle_t taskNetwork_handle = nullptr;				// 網絡任務
TaskHandle_t taskModeManagement_handle = nullptr;		// 模式管理任務
TaskHandle_t taskUART0Read_handle = nullptr;			// UART0讀取任務
TaskHandle_t taskServoSet_handle = nullptr;				// 伺服馬達調試任務
/* 定時器參照 */
TimerHandle_t wifiReconnectTimer; // WiFi重連定時器

static constexpr uint32_t WIFI_RECONNECT_DELAYS_MS[] = {5000, 15000, 30000, 60000};
static constexpr uint32_t WIFI_RECONNECT_JITTER_MS = 1000;
static std::atomic_bool wifiReconnectAllowed{false};
static std::atomic_uint32_t wifiReconnectAttempt{0};

void setup()
{
	uint8_t log_level = config.getLogConfig();
	if (log_level < ESP_LOG_ERROR || log_level > ESP_LOG_VERBOSE)
	{
		log_level = ESP_LOG_INFO;
		config.setLogConfig(log_level);
	}
	esp_log_level_set("*", static_cast<esp_log_level_t>(log_level));

	/* 系統資訊列印 */
	ESP_LOGI("System", "========================================");
	ESP_LOGI("System", "3rd Eyes System Starting...");
	ESP_LOGI("System", "Version: %s", VERSION);
	ESP_LOGI("System", "========================================");
	ESP_LOGI("System", "=== ESP32-S3 System Information ===");
	ESP_LOGI("System", "SDK Version: %s", ESP.getSdkVersion());
	ESP_LOGI("System", "Chip Model: %s", ESP.getChipModel());
	ESP_LOGI("System", "Chip Revision: %d", ESP.getChipRevision());
	ESP_LOGI("System", "CPU Frequency: %d MHz", ESP.getCpuFreqMHz());
	ESP_LOGI("System", "Flash Size: %d MB", ESP.getFlashChipSize() / 1024 / 1024);
	ESP_LOGI("System", "Flash Speed: %d MHz", ESP.getFlashChipSpeed() / 1000000);
	const char *flashModeStr;
	switch (ESP.getFlashChipMode())
	{
		case 0:
			flashModeStr = "QIO";
			break;
		case 1:
			flashModeStr = "QOUT";
			break;
		case 2:
			flashModeStr = "DIO";
			break;
		case 3:
			flashModeStr = "DOUT";
			break;
		default:
			flashModeStr = "Unknown";
			break;
	}
	ESP_LOGI("System", "Flash Mode: %s", flashModeStr);
	if (psramFound())
	{
		ESP_LOGI("System", "PSRAM Size: %d MB", ESP.getPsramSize() / 1024 / 1024);
	}
	else
	{
		ESP_LOGI("System", "PSRAM Size: PSRAM Not Enabled");
	}
	ESP_LOGI("System", "========================================");

	while (xTaskGetTickCount() < 2000)
	{
		; // 等待2秒
	}

	ESP_LOGI("UART", "UART0 init...");

	/* 佇列建立 */
	ESP_LOGI("quene", "quene create..."); // 打印佇列建立狀態

	queueCreate(&wit_data_quene, 10, sizeof(witData));							 // witData結構體佇列
	queueCreate(&wit_data_relative_angle_quene, 10, sizeof(witPProcessingData)); // witPProcessingData結構體佇列
	queueCreate(&eyesmove_data_quene, 10, sizeof(eyesMove_data));				 // eyesMove_data結構體佇列
	queueCreate(&gc9a01_data_quene, 10, sizeof(GC9A01_data));					 // GC9A01_data結構體佇列
	queueCreate(&wifiUpdate_data_quene, 10, sizeof(NetworkCommand));			 // WiFi更新佇列
	// 設定更新只保留最新值
	queueCreate(&wit_advanced_config_update_quene, 1, sizeof(AppConfig::AdvancedConfig));
	queueCreate(&gyroscope_advanced_config_update_quene, 1, sizeof(AppConfig::AdvancedConfig));
	queueCreate(&mode_data_quene, 1, sizeof(int8_t));							// 模式數據佇列
	queueCreate(&network_control_data_quene, 10, sizeof(network_control_data)); // 網絡控制佇列
	queueCreate(&network_control_speed_data_quene, 10, sizeof(double));			// 網絡控制速度佇列
	queueCreate(&servoSet_data_quene, 10, sizeof(servoSet_data));				// 伺服馬達數據佇列

	ESP_LOGI("quene", "quene create success"); // 打印佇列建立成功狀態

	witStopEventGroup = xEventGroupCreate();
	if (!witStopEventGroup)
	{
		ESP_LOGE("mode", "WIT stop event group create error");
		while (1)
		{
			vTaskDelay(1000);
		}
	}

	/* 定時器建立 */
	wifiReconnectTimer = xTimerCreate("wifiTimer", pdMS_TO_TICKS(15000), pdFALSE, (void *)0, TimerReconnectWiFi); // WiFi重連定時器

	/* 使能伺服電機 */
	eyesmove.eyesMove_init();
	gc9a01.GC9A01_init();
	gc9a01.GC9A01_setEyes_r(80, 1, 10);
}

void loop()
{
	static bool tasks_created = false;
	if (!tasks_created)
	{
		tasks_created = true;
		xTaskCreatePinnedToCore(taskUART0Read, "taskUART0Read", 4096, NULL, 3, &taskUART0Read_handle, 0);				 // 創建UART0讀取任務
		xTaskCreatePinnedToCore(taskNetwork, "taskNetwork", 8192, NULL, 1, &taskNetwork_handle, 0);						 // 創建網絡任務
		xTaskCreatePinnedToCore(taskGC9A01, "taskGC9A01", 8192, NULL, 1, &taskGC9A01_handle, 1);						 // 創建GC9A01任務
		xTaskCreatePinnedToCore(taskModeManagement, "taskModeManagement", 4096, NULL, 2, &taskModeManagement_handle, 1); // 創建模式管理任務
	}
	vTaskDelay(1000);
}

/** 事件相關函數 **/
void WiFiEvent(WiFiEvent_t event, WiFiEventInfo_t info)
{
	switch (event)
	{
		case ARDUINO_EVENT_WIFI_STA_CONNECTED:
			ESP_LOGI("wifi", "STA connected: SSID='%.*s', BSSID=%s, channel=%u, auth=%d", info.wifi_sta_connected.ssid_len,
					 reinterpret_cast<const char *>(info.wifi_sta_connected.ssid), macToString(info.wifi_sta_connected.bssid).c_str(),
					 info.wifi_sta_connected.channel, info.wifi_sta_connected.authmode);
			break;
		case ARDUINO_EVENT_WIFI_STA_GOT_IP:
			xTimerStop(wifiReconnectTimer, 0);
			wifiReconnectAttempt.store(0);
			ESP_LOGI("wifi", "Connected to '%s': BSSID=%s, channel=%d, RSSI=%d dBm, IP=%s", WiFi.SSID().c_str(), WiFi.BSSIDstr().c_str(),
					 WiFi.channel(), WiFi.RSSI(), WiFi.localIP().toString().c_str());
			break;
		case ARDUINO_EVENT_WIFI_STA_DISCONNECTED:
			ESP_LOGW("wifi", "STA disconnected: BSSID=%s, reason=%u (%s)", macToString(info.wifi_sta_disconnected.bssid).c_str(),
					 info.wifi_sta_disconnected.reason,
					 WiFi.STA.disconnectReasonName(static_cast<wifi_err_reason_t>(info.wifi_sta_disconnected.reason)));
			ScheduleWiFiReconnect(info.wifi_sta_disconnected.reason);
			break;
		case ARDUINO_EVENT_WIFI_STA_STOP:
			ESP_LOGI("wifi", "WiFi stopped");
			break;
		case ARDUINO_EVENT_WIFI_AP_START:
			ESP_LOGI("wifi", "SoftAP \'%s\' Started with IP %s", WiFi.softAPSSID().c_str(), WiFi.softAPIP().toString().c_str());
			break;
		case ARDUINO_EVENT_WIFI_AP_STACONNECTED:
			ESP_LOGI("wifi", "SoftAP station connected with MAC: %s, AID: %d", macToString(info.wifi_ap_staconnected.mac).c_str(),
					 info.wifi_ap_staconnected.aid);
			break;
		case ARDUINO_EVENT_WIFI_AP_STADISCONNECTED:
			ESP_LOGI("wifi", "SoftAP station disconnected with MAC: %s, AID: %d", macToString(info.wifi_ap_stadisconnected.mac).c_str(),
					 info.wifi_ap_stadisconnected.aid);
			break;
		case ARDUINO_EVENT_WIFI_AP_STOP:
			ESP_LOGI("wifi", "SoftAP stopped");
			break;
		default:
			break;
	}
}

/** 回調相關函數 **/
/* WiFi重連定時器回調 */
void TimerReconnectWiFi(TimerHandle_t xTimer)
{
	if (wifiReconnectAllowed.load() && WiFi.status() != WL_CONNECTED)
	{
		// Wi-Fi 操作集中於 network task，避免跨 task 修改 driver 狀態。
		const NetworkCommand command = NetworkCommand::StaReconnect;
		if (xQueueSend(wifiUpdate_data_quene, &command, 0) != pdTRUE)
		{
			ESP_LOGE("wifi", "Failed to queue WiFi reconnect command");
		}
	}
}

void ScheduleWiFiReconnect(uint8_t reason)
{
	if (!wifiReconnectAllowed.load())
	{
		return;
	}

	const uint32_t attempt = wifiReconnectAttempt.fetch_add(1);
	const size_t delayCount = sizeof(WIFI_RECONNECT_DELAYS_MS) / sizeof(WIFI_RECONNECT_DELAYS_MS[0]);
	const size_t delayIndex = attempt < delayCount ? attempt : delayCount - 1;
	const uint32_t delayMs = WIFI_RECONNECT_DELAYS_MS[delayIndex] + esp_random() % (WIFI_RECONNECT_JITTER_MS + 1);

	ESP_LOGW("wifi", "Reconnect attempt %lu scheduled in %lu ms after reason %u", static_cast<unsigned long>(attempt + 1),
			 static_cast<unsigned long>(delayMs), reason);
	if (xTimerChangePeriod(wifiReconnectTimer, pdMS_TO_TICKS(delayMs), 0) != pdPASS)
	{
		ESP_LOGE("wifi", "Failed to schedule WiFi reconnect timer");
	}
}

bool ConnectMeshWiFi(const AppConfig::WiFiConfig &wifiConfig)
{
	if (!wifiConfig.is_enabled || wifiConfig.ssid.isEmpty())
	{
		return false;
	}

	WiFi.setScanMethod(WIFI_ALL_CHANNEL_SCAN);
	WiFi.setSortMethod(WIFI_CONNECT_AP_BY_SIGNAL);
	const char *password = wifiConfig.password.isEmpty() ? nullptr : wifiConfig.password.c_str();

	if (WiFi.begin(wifiConfig.ssid.c_str(), password, 0, nullptr, false) == WL_CONNECT_FAILED)
	{
		ESP_LOGE("wifi", "Failed to configure STA credentials");
		return false;
	}

	wifi_config_t stationConfig{};
	esp_err_t error = esp_wifi_get_config(WIFI_IF_STA, &stationConfig);
	if (error != ESP_OK)
	{
		ESP_LOGE("wifi", "Failed to read STA configuration: %s", esp_err_to_name(error));
		return false;
	}

	// Mesh 選擇必須保留同一 SSID 下切換 BSSID 與頻道的自由。
	stationConfig.sta.scan_method = WIFI_ALL_CHANNEL_SCAN;
	stationConfig.sta.sort_method = WIFI_CONNECT_AP_BY_SIGNAL;
	stationConfig.sta.bssid_set = false;
	stationConfig.sta.channel = 0;
	stationConfig.sta.failure_retry_cnt = 1;

#if defined(CONFIG_ESP_WIFI_11KV_SUPPORT) && CONFIG_ESP_WIFI_11KV_SUPPORT
	stationConfig.sta.rm_enabled = 1;
	stationConfig.sta.btm_enabled = 1;
	static bool capabilityLogged = false;
	if (!capabilityLogged)
	{
		ESP_LOGI("wifi", "802.11k/v roaming assistance enabled");
		capabilityLogged = true;
	}
#else
	static bool capabilityLogged = false;
	if (!capabilityLogged)
	{
		ESP_LOGI("wifi", "802.11k/v unavailable; using multi-BSSID scan fallback");
		capabilityLogged = true;
	}
#endif

	error = esp_wifi_set_config(WIFI_IF_STA, &stationConfig);
	if (error != ESP_OK)
	{
		ESP_LOGE("wifi", "Failed to apply STA configuration: %s", esp_err_to_name(error));
		return false;
	}

	wifiReconnectAllowed.store(true);
	error = esp_wifi_connect();
	if (error != ESP_OK)
	{
		ESP_LOGE("wifi", "Failed to start STA connection: %s", esp_err_to_name(error));
		ScheduleWiFiReconnect(WIFI_REASON_UNSPECIFIED);
		return false;
	}

	ESP_LOGI("wifi", "Connecting to '%s' with multi-BSSID selection", wifiConfig.ssid.c_str());
	return true;
}

bool StartSoftAP(const AppConfig::SoftAPConfig &softAPConfig)
{
	const bool started = softAPConfig.password.isEmpty() ? WiFi.softAP(softAPConfig.ssid.c_str())
														 : WiFi.softAP(softAPConfig.ssid.c_str(), softAPConfig.password.c_str());
	if (!started)
	{
		ESP_LOGE("wifi", "Failed to start SoftAP");
	}
	return started;
}

/** 任務相關函數 **/
/* 網絡相關任務 */
void taskNetwork(void *pvParameters)
{
	NetworkCommand networkCommand = NetworkCommand::StaConfigUpdate;

	/* WiFi初始化 */
	WiFi.onEvent(WiFiEvent); // 註冊事件回呼
	WiFi.setAutoReconnect(false);
	WiFi.setSleep(WIFI_PS_MIN_MODEM);
	// SoftAP 與 STA 共用頻道，STA 重連期間不得重啟 SoftAP。
	WiFi.mode(WIFI_AP_STA);
	if (!StartSoftAP(config.getSoftAPConfig()))
	{
		vTaskDelete(NULL);
		return;
	}

	if (WiFi.getSleep() == WIFI_PS_MIN_MODEM)
	{
		ESP_LOGI("wifi", "WiFi power save mode: MIN_MODEM");
	}
	else
	{
		ESP_LOGW("wifi", "Failed to enable WiFi power save");
	}

	/* 伺服器任務創建 */
	xTaskCreatePinnedToCore(taskWebServer, "taskWebServer", 4096, NULL, 1, &taskWebServer_handle, 0); // 創建網絡任務

	while (1)
	{

		if (networkCommand == NetworkCommand::StaConfigUpdate)
		{
			AppConfig::WiFiConfig wificonfig = config.getWiFiConfig(); // 獲取WiFi配置

			wifiReconnectAllowed.store(false);
			wifiReconnectAttempt.store(0);
			xTimerStop(wifiReconnectTimer, 0);
			if (xTaskGetTickCount() > 5000) // 判斷初始化還是更新
			{
				ESP_LOGI("wifi", "Updating WiFi connection...");
				vTaskDelay(500);
			}

			WiFi.disconnect(false, true, 1000);
			if (wificonfig.is_enabled && !wificonfig.ssid.isEmpty())
			{
				ConnectMeshWiFi(wificonfig);
			}
			else
			{
				ESP_LOGI("wifi", "STA connection disabled; SoftAP remains active");
			}
		}
		else if (networkCommand == NetworkCommand::SoftAPConfigUpdate)
		{
			AppConfig::SoftAPConfig softapconfig = config.getSoftAPConfig(); // 獲取SoftAP配置

			ESP_LOGI("wifi", "Updating SoftAP configuration...");
			vTaskDelay(500);
			WiFi.softAPdisconnect();
			StartSoftAP(softapconfig);
		}
		else if (networkCommand == NetworkCommand::StaReconnect)
		{
			const AppConfig::WiFiConfig wificonfig = config.getWiFiConfig();
			if (wifiReconnectAllowed.load() && WiFi.status() != WL_CONNECTED && wificonfig.is_enabled && !wificonfig.ssid.isEmpty())
			{
				ESP_LOGI("wifi", "Attempting reconnect...");
				ConnectMeshWiFi(wificonfig);
			}
		}
		xQueueReceive(wifiUpdate_data_quene, &networkCommand, portMAX_DELAY); // 等待WiFi更新信號
	}
}

/* 伺服器相關任務 */
void taskWebServer(void *pvParameters)
{

	/* LittleFS啓動 */
	ESP_LOGI("LittleFS", "Mounting LittleFS...");
	if (!LittleFS.begin(false, "/littlefs", 10, "littlefs"))
	{
		ESP_LOGW("LittleFS", "LittleFS mount failed, formatting...");
		if (!LittleFS.begin(true, "/littlefs", 10, "littlefs"))
		{
			ESP_LOGE("LittleFS", "LittleFS format failed!");
			vTaskDelete(NULL);
			return;
		}
		ESP_LOGI("LittleFS", "LittleFS formatted successfully");
	}
	ESP_LOGI("LittleFS", "LittleFS mounted successfully");

	File webVersionFile = LittleFS.open("/www/version.txt", FILE_READ);
	if (!webVersionFile)
	{
		ESP_LOGE("System", "Web version file is missing or could not be opened");
	}
	else
	{
		String webVersion = webVersionFile.readString();
		webVersionFile.close();
		webVersion.trim();

		if (webVersion.length() == 0)
		{
			ESP_LOGW("System", "Web version file is empty");
		}
		else
		{
			ESP_LOGI("System", "Web Version: %s", webVersion.c_str());
			if (webVersion != VERSION)
			{
				ESP_LOGW("System", "Version mismatch: Firmware=%s, Web=%s", VERSION, webVersion.c_str());
			}
		}
	}

	// 顯示檔案系統資訊
	ESP_LOGI("LittleFS", "Total: %d bytes, Used: %d bytes", LittleFS.totalBytes(), LittleFS.usedBytes());

	/* mDNS啓動 */
	if (!MDNS.begin("3rdeyes"))
	{
		ESP_LOGE("mDNS", "mDNS failed to start!");
		vTaskDelete(NULL);
	}
	ESP_LOGI("mDNS", "mDNS started: http://3rdeyes.local");

	/* WebSocket服務器 */
	ws.onEvent(onSocketEvent); // 設置WebSocket事件處理函數

	/* 設置Web服務器路由 */
	server.addHandler(&ws); // 將WebSocket服務器添加到Web服務器
	server.serveStatic("/", LittleFS, "/www/").setDefaultFile("index.html");
	server.onNotFound(handleNotFound);
	server.on("/", HTTP_GET, handleRoot);
	server.on("/api/version", HTTP_GET, api_version);
	server.on("/api/wifi_config", HTTP_GET, api_wifi_config);
	server.on("/api/set_wifi_config", HTTP_POST, [](AsyncWebServerRequest *request) {}, NULL, api_set_wifi_config);
	server.on("/api/softap_config", HTTP_GET, api_softAP_config);
	server.on("/api/set_softap_config", HTTP_POST, [](AsyncWebServerRequest *request) {}, NULL, api_set_softAP_config);
	server.on("/api/mode_config", HTTP_GET, api_mode_config);
	server.on("/api/set_mode_config", HTTP_POST, [](AsyncWebServerRequest *request) {}, NULL, api_set_mode_config);
	server.on("/api/advanced_config", HTTP_GET, api_advanced_config);
	server.on("/api/set_advanced_config", HTTP_POST, [](AsyncWebServerRequest *request) {}, NULL, api_set_advanced_config);
	server.on("/api/servo_config", HTTP_GET, api_servo_config);
	server.on("/api/set_servo_config", HTTP_POST, [](AsyncWebServerRequest *request) {}, NULL, api_set_servo_config);

	/* 伺服器啓動 */
	server.begin();
	ESP_LOGI("server", "HTTP server started");
	while (1)
	{
		ws.cleanupClients();
		vTaskDelay(1000);
	}
}
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

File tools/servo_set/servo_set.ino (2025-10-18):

#include <ESP32Servo.h>

#define UPPER_EYELID_PIN 13 // 上眼皮伺服馬達引脚
#define LOWER_EYELID_PIN 14 // 下眼皮伺服馬達引脚
#define EYEBALL_PIN 21		// 眼球伺服馬達引脚

Servo upper_eyelid_servo; // 上眼皮伺服馬達
Servo lower_eyelid_servo; // 下眼皮伺服馬達
Servo eyeball_servo;	  // 眼球伺服馬達

void setup()
{
	upper_eyelid_servo.attach(UPPER_EYELID_PIN); // 附加上眼皮伺服馬達
	lower_eyelid_servo.attach(LOWER_EYELID_PIN); // 附加下眼皮伺服馬達
	eyeball_servo.attach(EYEBALL_PIN);			 // 附加眼球伺服馬達

	// 設置伺服馬達的初始位置
	upper_eyelid_servo.write(90); // 上眼皮初始位置
	lower_eyelid_servo.write(90); // 下眼皮初始位置
	eyeball_servo.write(90);	  // 眼球初始位置
}

void loop()
{
}

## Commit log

2025-03-25 添加初始化眼睛函數
2025-04-03 wit程式庫初始化代碼
2025-04-06 數據讀取
2025-04-06 wit獲取Serial
2025-04-06 獲取wit資料
2025-04-08 差角計算
2025-04-10 GC9A01初始化
2025-04-11 適配眼睛
2025-04-12 伺服馬達初始化除錯
2025-04-16 wit移除磁場讀取，添加四元數讀取
2025-04-17 眼睛轉動實驗
2025-04-17 witData結構體四元數更改
2025-04-18 差角四元數計算
2025-04-18 去除四元數除錯資訊
2025-04-18 檔案目錄整理
2025-04-20 眼睛半徑動態效果
2025-04-21 眼睛光暈動態效果
2025-04-21 動態效果四捨五入
2025-04-22 眼睛光暈使用佇列傳參
2025-04-23 添加獲取眼珠參數函數
2025-04-23 設置眼珠半徑和光暈墻
2025-04-24 優化眼睛伺服器轉動範圍
2025-04-25 陀螺儀加速度處理
2025-04-25 陀螺儀處理結果傳遞變更（增加加速度）
2025-04-27 眼睛角度優化
2025-04-27 上傳.gitignore
2025-04-27 伺服電機限位獨立變數
2025-05-01 class縮行變更
2025-05-05 pid控制邏輯創建
2025-05-05 pid主程式控制
2025-05-06 優化眼珠防撞墻
2025-05-07 眼睛舵機角度墻優化
2025-05-07 佇列建立優化
2025-05-07 主程式檔名變更main
2025-05-07 眼睛移動更新優化
2025-05-09 優化眼鏡更新邏輯
    將上次更新次數改為記錄上次更新時間
2025-05-09 陀螺儀跟蹤模式
2025-05-19 優化眼睛跟蹤運動
2025-05-21 wit角速度差值計算
2025-05-23 修復眼睛半徑不動的bug
2025-05-23 眼睛光環隨角速度變化
2025-05-28 角度墻變更
2025-05-28 上傳pcd
    [3rd_eyes.SchDoc, 3rd_eyes_BOM.csv, GC9A01.PcbDoc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]
2025-05-30 亂碼符號修正
    [3rd_eyes_BOM.csv, GC9A01_BOM.csv]
2025-05-31 witread工具上傳
2025-06-01 pcd文檔上傳
2025-06-01 上傳src文檔
2025-06-01 上傳PCD協議
2025-06-01 3D模型上傳
    [01.prt, 01.stl, 02.prt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]
2025-06-01 3d模型文档及协议上传
2025-06-02 文檔作者完善
2025-06-02 專案readme更新
2025-06-02 專案發佈
2025-06-02 修復z軸方向反了問題
2025-06-02 v1.0.1版本發佈
2025-06-02 更新pcd文档错误
2025-06-03 添加在綫查看地址
2025-06-07 變更硬件程式碼結構
2025-06-07 .gitgnore移動
2025-06-07 更新arduino readme
2025-06-07 更新項目架構readme
2025-08-05 修改心形模型 (#1)
    * 心形模型更新
    添加孔以方便用軋帶固定
    * 文檔更新
    [heartShaped_dowm.prt, heartShaped_dowm.stl]
2025-10-18 添加網絡控制 (#2)
    添加了網絡控制，可以切換成網絡控制模式和陀螺儀跟蹤模式，并且提供網絡相關的設定
2025-10-18 版本發佈
2025-10-25 遷移硬體框架到platformIO (#3)
    遷移硬體框架從arduino到platformIO
    遷移文件系統從ffat到littlefs
    [n16r8.csv]
2025-10-25 版本發佈
    v1.2.0
2025-10-29 Change build output folder in readme
    Updated the build output folder from 'arduino' to 'platformIO'.
2025-11-02 添加readme图片
    添加焊接参考
2025-11-03 重構網頁框架 (#4)
    重構網頁框架，讓網頁更加容易維護
    添加進入網頁時加載提示
2025-11-10 自動設置陀螺儀 (#5)
    自動設置陀螺儀
    修復prefs占用資源問題
2025-11-10 版本發佈
    v1.2.1
2025-11-19 更新readme
    Updated installation instructions for servo and added images for clarity.
2026-03-21 更新18650版本 (#6)
    [02.prt, 02.stl, 03-1.prt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]
